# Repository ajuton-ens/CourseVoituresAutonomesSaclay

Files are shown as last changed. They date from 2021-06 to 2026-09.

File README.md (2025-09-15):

# Course de Voitures Autonomes Paris-Saclay CoVAPSy
Ce dépôt regroupe les documents et ressources liées à la course de voitures autonomes 1/10ème de Paris Saclay : https://ajuton-ens.github.io/CourseVoituresAutonomesSaclay/

Il est possible de s'inscrire ou d'obtenir plus d'informations en envoyant un mail à : anthony.juton@ens-paris-saclay.fr 

Le dossier _Simulator_ propose un simulateur Webots R2023b avec une voiture TT-02 équipée d'un lidar.
L'Efrei a aussi déposé un simulateur Webots.

Les cartes électroniques (pdf et fichiers Eagle) et les pièces mécaniques (fichiers step) de la voiture type sont dans le dossier _Hardware_.

---------------------------------------------
# Autonomous Car Race Paris-Saclay CoVAPSy

This repository contains documents and resources related to the 1/10th self-driving car race in Paris-Saclay: https://ajuton-ens.github.io/CourseVoituresAutonomesSaclay/

You can register or obtain more information by sending an email to: anthony.juton@ens-paris-saclay.fr

The folder _Simulator_ includes a Webots R2023b simulator with a TT-02 car equipped with a lidar.
Efrei has also submitted a Webots simulator.

The electronic boards (PDF and Eagle files) and mechanical parts (Step files) for the typical car are in the folder _Hardware_.

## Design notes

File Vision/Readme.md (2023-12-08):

# Dossier regroupant les expériences sur la vision : algorithmes et caméras

# Caméra RPI2
Fonctionne bien avec RPI4 et Jetson nano (connecteur pour caméra RPI sur la JN30D).

# Realsense 435i
Caméra RGBD

# Huskylens
Caméra avec l'IA intégré. C'est très fermé et il est difficile de faire autre chose que les exemples fournis. Résultats décevant sur son exploitation pour les voitures en 2023

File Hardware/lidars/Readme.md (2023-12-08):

# Document recensant les expériences Lidar

## Slamtec RpLidar A2M8
115200 bauds, 10 tours/seconde, 200 points par tour en mode express scan avec le module python rplidar-roboticia
Juste 80 points par tour en mode scan normal.
Attention, le lidar envoyant en continu, il faut recevoir en continu, sous peine de laisser le buffer de réception déborder.

## Slamtec RpLidar A2M12
256000 bauds, 10 tours/seconde, 300 points par tour en mode express scan avec le module python rplidar-roboticia

## Slamtec RpLidar A3M12
tourne plus vite, pas testé

## Slamtec RpLidar S2
1 Mbit/s trop de données pour être utilisé en python. Résultats prometteurs avec le noeud ROS2 associé (écrit en C/C++ certainement).

## Slamtec RpLidar S3
tourne plus vite, pas testé

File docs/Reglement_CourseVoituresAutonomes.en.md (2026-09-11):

# Paris-Saclay Autonomous Car Race Rules (CoVAPSy)

These rules evolve from year to year; feel free to send your comments and suggestions.

## The Vehicle

The vehicle must use a Tamiya TT02 chassis/motor kit and, for propulsion, a NiMH 7.2V battery with a maximum capacity of 5000 mAh. A secondary battery, of any type, is allowed to power the electronics. Powering the motor with a voltage higher than the battery voltage is not allowed. The car must have a body covering more than 80% of it (estimated by the jury in a non-scientific way...).
The vehicle, with all its sensors and actuators, must fit within the dimensions below:

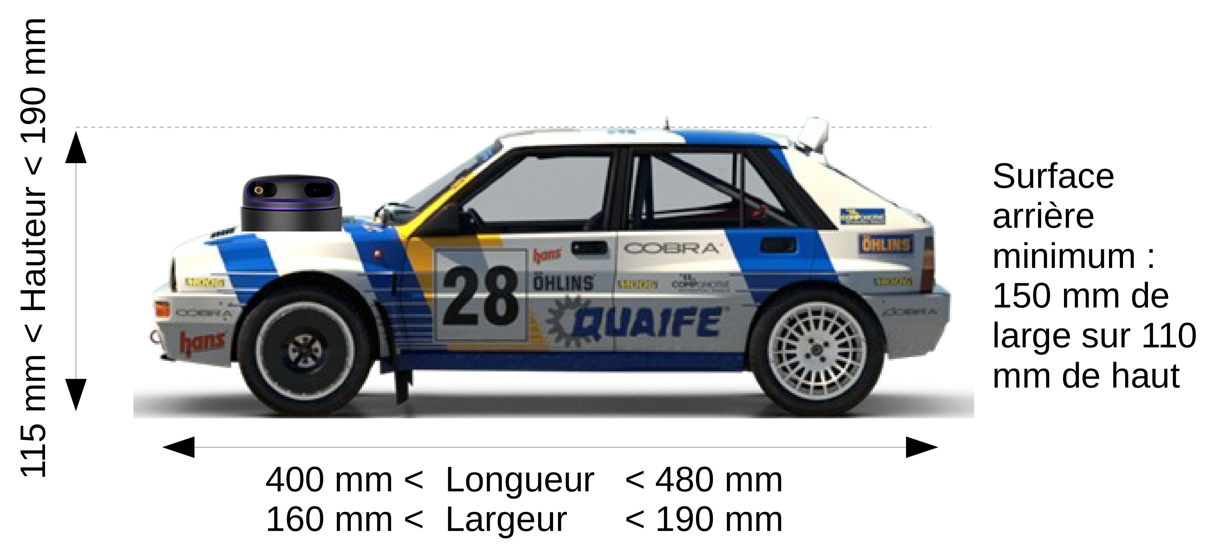
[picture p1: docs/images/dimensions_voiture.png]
car dimensions diagram


The car must be visible to vehicles following it: the car must have at least one opaque rectangle at the rear, 150 mm wide and 110 mm high. Only a small gap (< 10 mm high) for ground clearance is allowed.
Transparent bodies or those with green, red, or gray as the main color are not allowed. Guides for painting the car are available on YouTube (e.g., https://www.youtube.com/watch?v=MO5J6AqEpbs). A test with an RP-Lidar A2M12 or A2M8 validates the rear visibility of the car. If not detected (some black paints absorb infrared), off-white tape will be added to the rear of the car.

It is possible to remove the front-wheel drive to improve turning radius.

The car must be able to operate in both forward and reverse.

To improve steering mechanics, some plastic parts may be replaced with commercially available aluminum parts (Yeah Racing TATT-S03BU available at Rcmart.com or Tamiya kit 54574 sold at Conrad).
Any major modification to the chassis (beyond a few drillings) must be requested and approved by the other institutions participating in the race. The request must include references or plans of the intended modifications.

Team communication with the vehicle must be limited to sending a start signal and a stop signal. The vehicle may send information to the team (telemetry). Sending commands that modify the vehicle's behavior will result in team disqualification. For the 2026 edition, the use of a trackside computer is permitted at the end of remote calculations. Obviously, teams cannot touch this computer once the start has been announced..

A standard car kit is available (see *Standard Car* menu) from the Ménagerie Technologique.

## The Track

The track layout is not known before the day of the competition. Providing the car with information about the track layout is prohibited. Referees may check this, for example, on an auxiliary track. The car may learn the track by completing up to 3 setup laps.

The track consists of 200 mm high borders, green on the right in the direction of travel and red on the left in one direction, and vice versa in the opposite direction. These borders are made of straight elements and arcs with a curvature radius R = 400 mm or more. The floor is gray linoleum. The track is at all points wider than 700 mm but may contain obstacles inside.

Color references:

* GREEN: RAL 6024
* RED: RAL 3020
* FLOOR: PVC GERFLOR concrete effect leone anthracite l.4 m Ref 83309786 (Leroy Merlin)

Color references are approximate, and the track edges may be marked by impacts.

Here is an example of one of the 2023 tracks:

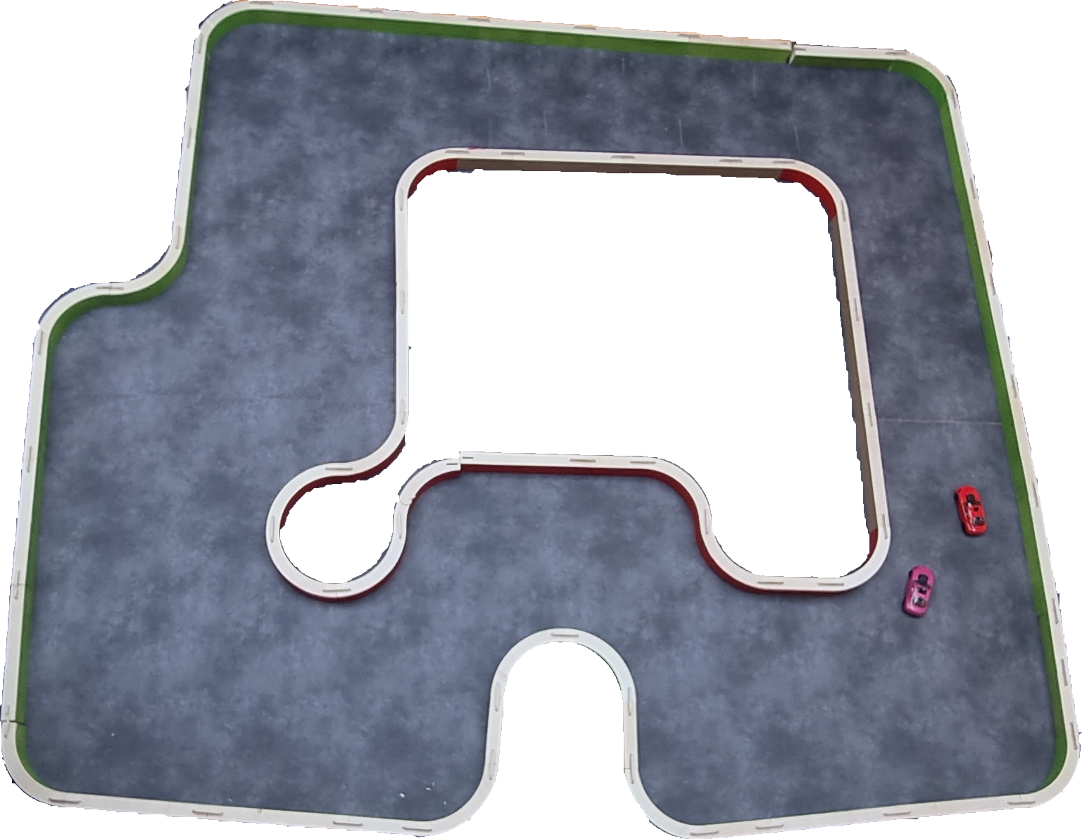
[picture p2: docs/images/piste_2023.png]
example track layout


A track kit is available from the Ménagerie Technologique.

## Homologation

Homologation is done in 4 steps:

* validation of vehicle elements (dimensions, battery, chassis, lidar-detectable color, etc.),
* validation of remote start and stop,
* verification of the vehicle's ability to move along a straight track section plus a curve without touching the borders,
* verification of the vehicle's ability to reverse in case of blockage against an obstacle and in the absence of a vehicle behind.
* verification of the vehicle's ability to avoid an obstacle (with the size of a car) on a section of track.

The referees may consider homologation with a penalty for minor rule violations: for example, a vehicle that does not stop or reverse properly.

For both races and qualifications, a car using SLAM may complete up to 3 setup laps, without obstacles. Obstacles or opponent cars are added afterward, once the car is on the starting grid.

## Qualifications 1 – Time Trial

The first qualification phase consists of 2 runs with a single car on track A, which includes fixed obstacles similar in size to a car.
For each run, the car completes 2 laps. The best of the 2 times is kept, to compensate for any technical issue during the first run. One of the passages is clockwise and the second is counterclockwise.

If the car fails to complete both laps on both attempts, a time of 120 seconds is recorded if the car completed one lap, and 180 seconds if it did not complete even one lap.

At the end of the first qualification phase, the first car gets 25 points, the second 24 points, and so on down to a minimum of 5 points for any car with less than 120 s. A car that has completed just one lap (time of 120s) gets one point.

## Qualifications 2 – Races

The second qualification phase consists of 2 group races with 4 to 8 cars over 3 laps on track B and 3 laps on track C (one clockwise and the other counterclockwise). The method for forming the N groups is based on the qualification ranking (group n is composed of cars ranked n%N, where n is the group number and N is the number of groups). In each race, the car accumulates points for the overall qualification ranking: 10 points for the first, 8 points for the 2nd, 6 for the 3rd, 4 for cars that completed all 3 laps and 1 point for cars that did not finish the race.

For each race (including the final):

* Teams have 3 minutes to set up their vehicle on the track.
* All vehicles in the group are positioned on the starting grid according to qualification results.
* Once all teams have declared they are ready, it is forbidden to touch the vehicles. The referee gives the start signal orally.
* The finishing order is recorded after a predefined number of laps (3 by default for qualification, 5 for finals).
* A car that does not complete the required number of laps is not ranked.

The referee and race marshals ensure the proper conduct of the races:

* A vehicle displaying clearly aggressive behavior towards opponents is disqualified and removed from the track, as is a car deliberately preventing another from overtaking.
* A vehicle immobilized on the track for more than 10 seconds, without being blocked by another car, is removed from the track.
* A vehicle that travels more than 2 m in the wrong direction is removed from the track.

## Final Phases – Races, in 2 Rounds

After the qualifications, each car receives 2 scores:

* the total coursesQualif (sum of points earned in the 2 qualification races)
* the total CLM+courseQualif (the previous score plus the points earned in the time trial qualification).

2 rounds are each composed of 3 races.

The top 2 of each group (by coursesQualif score, with CLM+courseQualif used to break ties) compete in race 1 of each round, the 3rd and 4th in race 2, and the others in race 3. The qualification ranking (by coursesQualif, with CLM+courseQualif as a tiebreaker) determines the starting grid, with the car with the most points starting at the front.

Referees record the finishing order after a predefined number of laps (5 by default) and award points as follows: 25 pts for 1st, 18 pts for 2nd, 15 pts for 3rd, 12 pts for 4th; 10 pts for 5th, 8 pts for 6th; 6 pts for 7th, 4 pts for 8th; 2 pts for 9th and 1 pt for 10th. A car that does not complete the required number of laps gets 0 points. Once the cars in the first race are ranked, points are then awarded to the cars in the second race, and so on.

The final ranking is based only on the points from the 2 final races. In case of a tie, the CLM+courseQualif score is used for the final ranking. If there is still a tie, the coursesQualif score is used.

Prizes are awarded to the 1st, 2nd, and 3rd in the overall ranking. There is also an innovation prize and a prize for the top license teams.

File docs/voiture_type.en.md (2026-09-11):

# Standard Car for the Paris-Saclay Autonomous Car Race

A standard car is offered for the autonomous car race. The complete kit and the kit containing {electronic boards, specific mechanical parts} have been available for purchase since January 2023, especially for teams without mechanical and/or electronic manufacturing capabilities.

This standard car is just an example to help teams get started. It is meant to be improved and expanded.

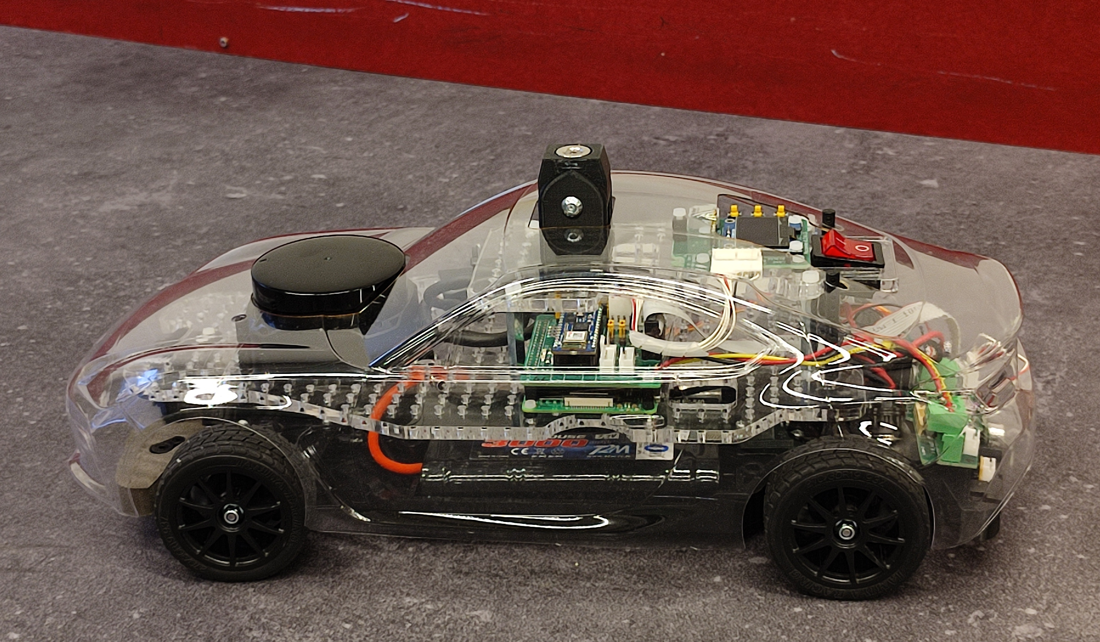
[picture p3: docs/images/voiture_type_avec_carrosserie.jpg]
standard car with body


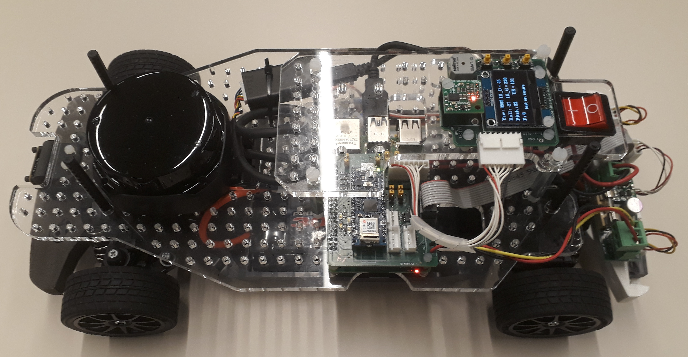
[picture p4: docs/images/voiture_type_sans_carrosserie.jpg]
standard car without body


## Control System

The block diagram of the control system is as follows, with several options for lidars, cameras, single-board computers, or microcontrollers:

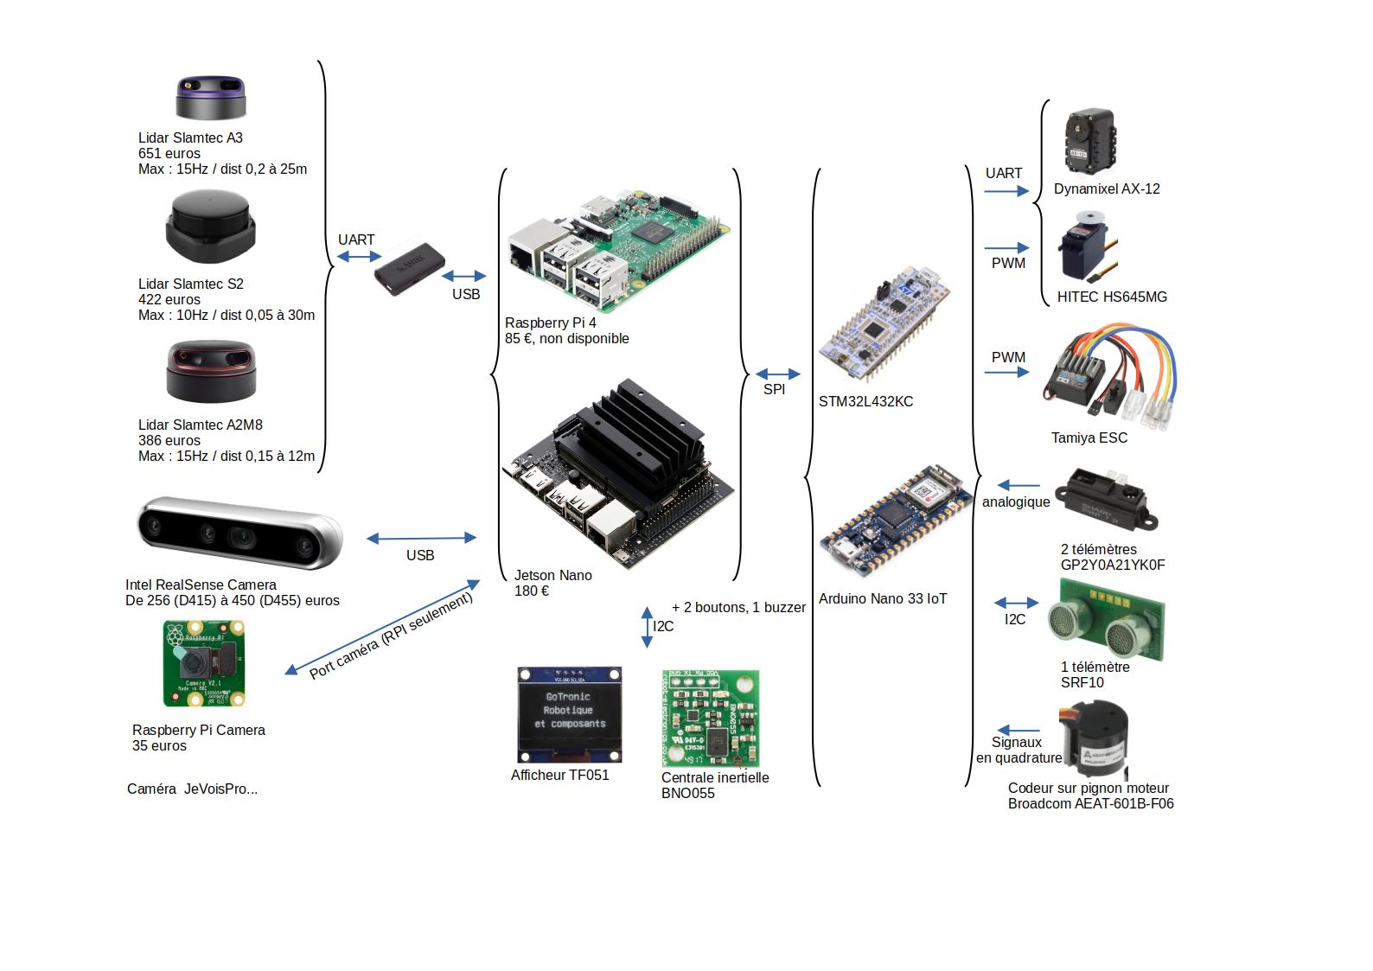
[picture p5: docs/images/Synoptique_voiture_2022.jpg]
block diagram of a standard car


The electronic schematics in Eagle and PDF format are provided in the _Hardware_ folder of the [Git repository](https://github.com/ajuton-ens/CourseVoituresAutonomesSaclay)

## Mechanics

Mechanical parts allow the TT-02 chassis to be adapted to these control system components. STL files are provided in the _Hardware_ folder of the [Git repository](https://github.com/ajuton-ens/CourseVoituresAutonomesSaclay)

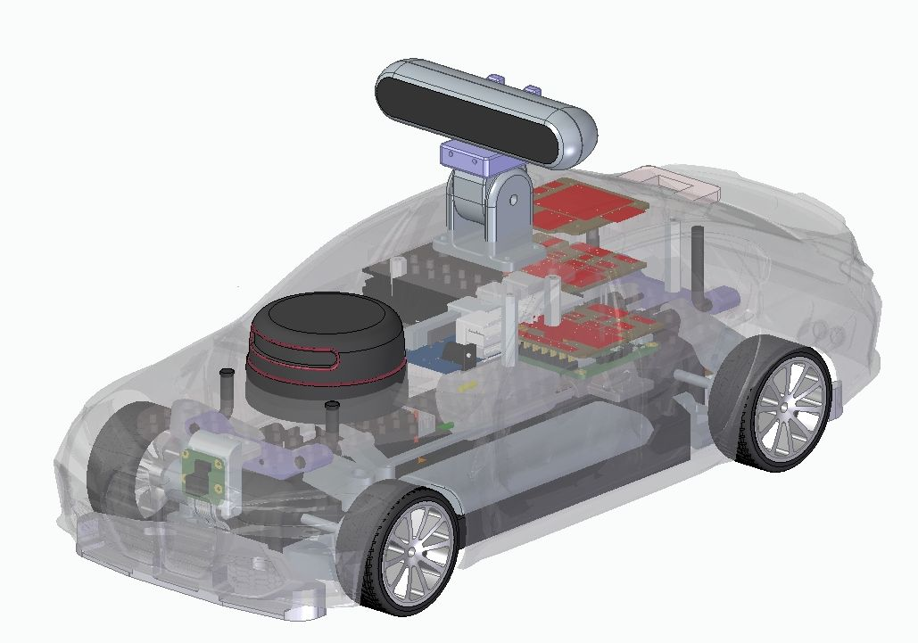
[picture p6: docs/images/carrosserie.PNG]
view with body of the standard car with Realsense camera


In addition to custom bodywork, the main feature of this kit is the modification of the drive shaft gear, the addition of an optical fork, and a new housing to allow measurement of the motor speed.

The kit notably offers the possibility to use a digital AX-12 servo motor instead of the standard analog servo.

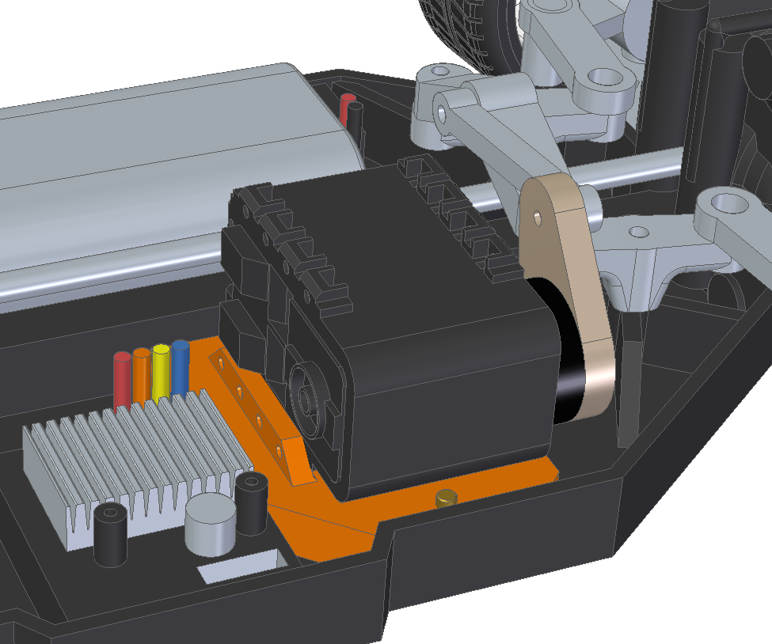
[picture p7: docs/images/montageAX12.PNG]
close-up of the AX-12 servo motor adaptation


Finally, the 3D parts allow for proper mounting of sensors at the front (Raspberry camera) and at the rear (IR and/or ultrasonic rangefinders).

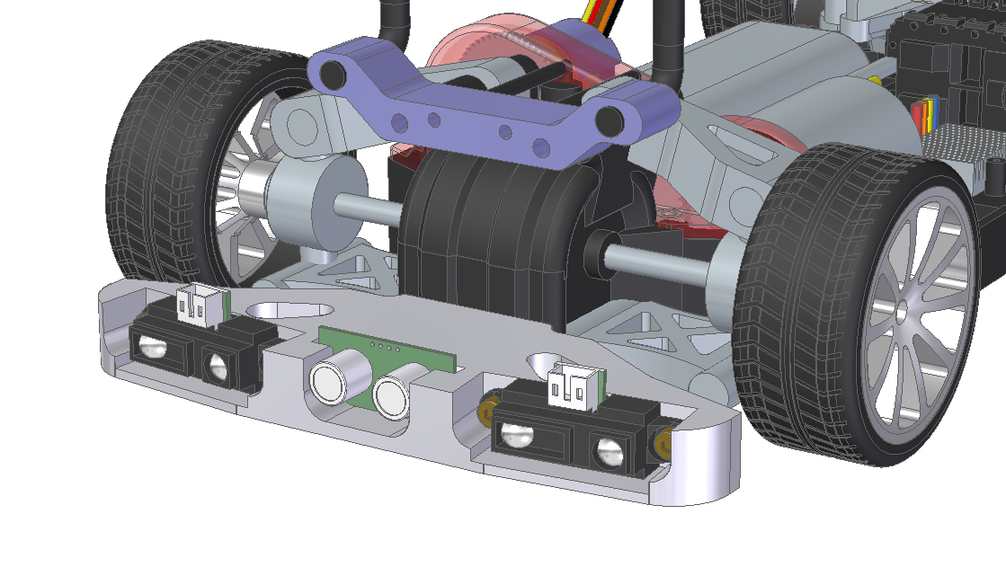
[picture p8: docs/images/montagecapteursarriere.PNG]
close-up of rear sensor mounting


## Parts List 2021

Here is a list of equipment, suppliers, and indicative prices (including VAT).

* Tamiya TT-02 Toyota GR 86 KIT	ref 58694 - RCTeam 58694 - €134.90
* Konect Servo 9kg 0.13s Digital KN-0913LVMG - RCTeam KN-0913LVMG - €19.90
* ORION Charger IQ801 1A - RCTeam ORI30197 - €15.90
* T2M Battery 7.2v Nimh 3000mah - RCTeam T1006300 - €27.30
                                
* Raspberry Pi 4 Model B - Kubii PI48GB - €94.50
* Official Black Micro-HDMI to HDMI Cable 1M - Kubii SC0270 - €4.80
* Micro-SD Card Class 10 32 GB - Kubii KG32_DEL - €8.94
* Official Power Supply for Raspberry Pi 4 15.3W USB-C - Kubii ALIMPI4 - €9.60
* Camera Module v2 8MP - Kubii 2510728 - €25.80
* Ribbon Cable for Raspberry Pi Camera 30 cm - Kubii kub1645-PRD - €0.96

* RPLIDAR A2M12 360 Laser Scanner Slamtec A2-M12 - Roboshop RB-Rpk-22 - €269.03
* USBA – microUSB Cable 20 cm - RS 182-8869 - €3.14

* Sonar Module SRF10 Devantech - Roboshop RB-Dev-10 - €36.86
* Absolute Orientation Module 9 DOF BNO055 Devantech - Roboshop RB-Dev-91 - €31.73
* Nucleo-G431KB Microcontroller Board - Farnell 3132398 - €10.89
* RS PRO USB Cable, Micro-USB B to USB A, 0.5m - RS 236-9078 - €2.89	
* Optical Fork with cables OPTEK TECHNOLOGY OPB815WZ - Farnell 1497919 - €5.39

* **Total for off-the-shelf modules**								~€725

## Parts List 2026

* Tamiya TT-02 Ford Mustang GT4 KIT ref 58664 - RCTEAM 58664 - 129,90 €
* Tamiya Pièce de Direction alu TT-02 54752 - RCTEAM 54752 - 67,20 €
* SkyRC Chargeur Nimh eN18 1.2A - RCTeam SK100184-01 - 19,90 €
* Robitronic Chargeur Peak Charger NiMh 1A - RCTEAM R01018 - 15,90 €
* Absima Batterie NIMH 7.2V 4200mAh - RCTeam 4100012 - 2 x 23,90 €

* Raspberry Pi 5 8 Go - Kubii - 204 €
* Ventilateur dissipateur officiel pour Raspberry Pi 5 - Kubii - 6 €
* Câble Micro-HDMI vers HDMI (type A) 1M pour PI4 - Kubii - 4,50 €
* Carte Micro-SD SanDisk Classe 10 - Kubii - 16,20 €
* Module caméra v3 Raspberry Pi grand angle - Kubii - 39 €
* Nappe Cable pour Raspberry Pi Camera 30 cm - Kubii - 2,40 €

* servomoteur HerkuleX DRS-0101 - Roboshop RB-Das-05 - 76,4 €
* SLAMTEC RPLIDAR C1 Scanner Laser DTOF 360°  - Roboshop RB-Rpk-35 - 75,3 €

* Module Sonar SRF10 Devantech - Gotronic 24506 - 19,90 €
* Carte microcontrôleur Nucleo-G431KB - Farnell 3132398 - 17,76 €
* Câble USB RS PRO, Micro-USB B vers USB A, 0.5m - RS 236-9078 - 2,86 €	
* Fourche optique, avec câbles	OPTEK TECHNOLOGY OPB815WZ - Farnell 1497919 - 4,54 €

* **Total for off-the-shelf modules**								~745 €

**Options:**

It is possible to replace the Raspberry Pi single-board computer with a Jetson Orin GPU board. Qualcomm/Thundercomm also offers a similar board, the Rubik Pi 3.

Camera RGBD to be placed on the roof:

* Realsense D435i Camera - Digikey 2311-82635D435IDKMP-ND - €445.54

The Ménagerie Technologique offers all the electronic boards for the standard car for €350 and all the mechanical parts for 250 €.

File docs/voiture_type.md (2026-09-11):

# Voiture type pour la course de voitures autonomes de Paris Saclay

Une voiture type est proposée pour la course de voitures autonomes. Le kit complet et le kit {cartes électroniques, pièces mécaniques spécifiques} sont disponibles à la vente depuis janvier 2023, notamment pour des équipes sans moyens de fabrication mécanique et/ou électronique.

Cette voiture type n'est qu'un exemple pour aider les équipes à démarrer. Il ne demande qu'à être enrichi.

voiture type avec sa carrosserie

voiture type sans sa carrosserie

## Contrôle-commande

Le schéma synoptique de la partie contrôle-commande est le suivant, avec plusieurs possibilités de lidars, caméras, nano-ordinateurs ou micro-contrôleurs : 

synoptique d'une voiture type

Les schémas électroniques au format Eagle et en pdf sont fournis dans le dossier _Hardware_ du [dépôt Git](https://github.com/ajuton-ens/CourseVoituresAutonomesSaclay)

## La mécanique

Des pièces mécaniques permettent d'adapter le châssis TT-02 à ces équipements de contrôle-commande. Les fichiers stl sont fournis dans le dossier _Hardware_ du [dépôt Git](https://github.com/ajuton-ens/CourseVoituresAutonomesSaclay)

vue avec carrosserie de la voiture type avec caméra Realsense

Outre les découpes propres de carrosserie, l'élément majeur de ce kit est la modification de la roue dentée de l'axe de transmission, l'ajout d'une fourche optique et d'un nouveau carter pour permettre la mesure de la vitesse du moteur.

Le kit propose notamment la possibilité d'utiliser un servo-moteur numérique AX-12 à la place du servo-moteur analogique standard.

zoom sur l'adaptation pour servo-moteur AX-12

Enfin, les pièces 3D permettent une fixation propre des capteurs à l'avant (caméra Raspberry) comme à l'arrière (télémètres IR et/ou ultrason).

zoom sur la fixation des capteurs à l'arrière

## Liste du matériel version 2021

Voici une liste de matériel, de fournisseurs et de prix TTC indicatifs.

* Tamiya TT-02 Toyota GR 86 KIT	ref 58694 - RCTeam 58694 - 134,90 €
* Konect Servo 9kg 0.13s Digital KN-0913LVMG - RCTeam KN-0913LVMG - 19,90 €
* ORION Chargeur IQ801 1A - RCTeam ORI30197 - 15,90 €
* T2M Accu 7.2v Nimh 3000mah - RCTeam T1006300 - 27,30 €

* Raspberry Pi 4 modèle B - Kubii PI48GB - 94,50 €
* Câble officiel noir Micro-HDMI vers HDMI 1M - Kubii SC0270 - 4,80 €
* Carte Micro-SD Classe 10 32 GB - Kubii KG32_DEL - 8,94 €
* Alimentation Officielle pour Raspberry Pi 4 15.3W USB-C - Kubii ALIMPI4 - 9,60 €
* Module Caméra v2 8MP - Kubii 2510728 - 25,80 €
* Nappe Cable pour Raspberry Pi Camera 30 cm - Kubii kub1645-PRD - 0,96 €

* Scanner à distance laser RPLIDAR A2M12 360 Slamtec A2-M12 - Roboshop RB-Rpk-22 - 269,03 €
* Câble USBA – microUSB 20 cm - RS 182-8869 - 3,14 €

* Module Sonar SRF10 Devantech - Roboshop RB-Dev-10 - 36,86 €
* Module d'Orientation Absolue 9 DOF BNO055	Devantech - Roboshop RB-Dev-91 - 31,73 €
* Carte microcontrôleur Nucleo-G431KB - Farnell 3132398 - 10,89 €
* Câble USB RS PRO, Micro-USB B vers USB A, 0.5m - RS 236-9078 - 2,89 €	
* Fourche optique, avec câbles	OPTEK TECHNOLOGY OPB815WZ - Farnell 1497919 - 5,39 €

* **Total des modules sur étagère**								~725 €

## Liste du matériel version 2026

* Tamiya TT-02 Ford Mustang GT4 KIT ref 58664 - RCTEAM 58664 - 129,90 €
* Tamiya Pièce de Direction alu TT-02 54752 - RCTEAM 54752 - 67,20 €
* SkyRC Chargeur Nimh eN18 1.2A - RCTeam SK100184-01 - 19,90 €
* Robitronic Chargeur Peak Charger NiMh 1A - RCTEAM R01018 - 15,90 €
* Absima Batterie NIMH 7.2V 4200mAh - RCTeam 4100012 - 2 x 23,90 €

* Raspberry Pi 5 8 Go - Kubii - 204 €
* Ventilateur dissipateur officiel pour Raspberry Pi 5 - Kubii - 6 €
* Câble Micro-HDMI vers HDMI (type A) 1M pour PI4 - Kubii - 4,50 €
* Carte Micro-SD SanDisk Classe 10 - Kubii - 16,20 €
* Module caméra v3 Raspberry Pi grand angle - Kubii - 39 €
* Nappe Cable pour Raspberry Pi Camera 30 cm - Kubii - 2,40 €

* servomoteur HerkuleX DRS-0101 - Roboshop RB-Das-05 - 76,4 €
* SLAMTEC RPLIDAR C1 Scanner Laser DTOF 360°  - Roboshop RB-Rpk-35 - 75,3 €

* Module Sonar SRF10 Devantech - Gotronic 24506 - 19,90 €
* Carte microcontrôleur Nucleo-G431KB - Farnell 3132398 - 17,76 €
* Câble USB RS PRO, Micro-USB B vers USB A, 0.5m - RS 236-9078 - 2,86 €	
* Fourche optique, avec câbles	OPTEK TECHNOLOGY OPB815WZ - Farnell 1497919 - 4,54 €

* **Total des modules sur étagère**								~745 €

**Options :**

Il est possible de remplacer le nano-ordinateur Raspberry Pi par une carte GPU Jetson Orin. 

Qualcomm/Thundercomm propose aussi une carte similaire, la rubik Pi 3

Caméra RGBD à placer sur le toit : 

* Caméra Realsense D435i - Digikey 2311-82635D435IDKMP-ND - 445,54 €

La ménagerie technologique propose l'ensemble des cartes électroniques de la voiture type pour 350 € et l'ensemble des pièces mécaniques pour 250 €

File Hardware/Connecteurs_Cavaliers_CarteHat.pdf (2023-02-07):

Origine de l’alimentation 3V3 :
A gauche, elle est issue de la carte microcontrôleur (à utiliser si il n’y a

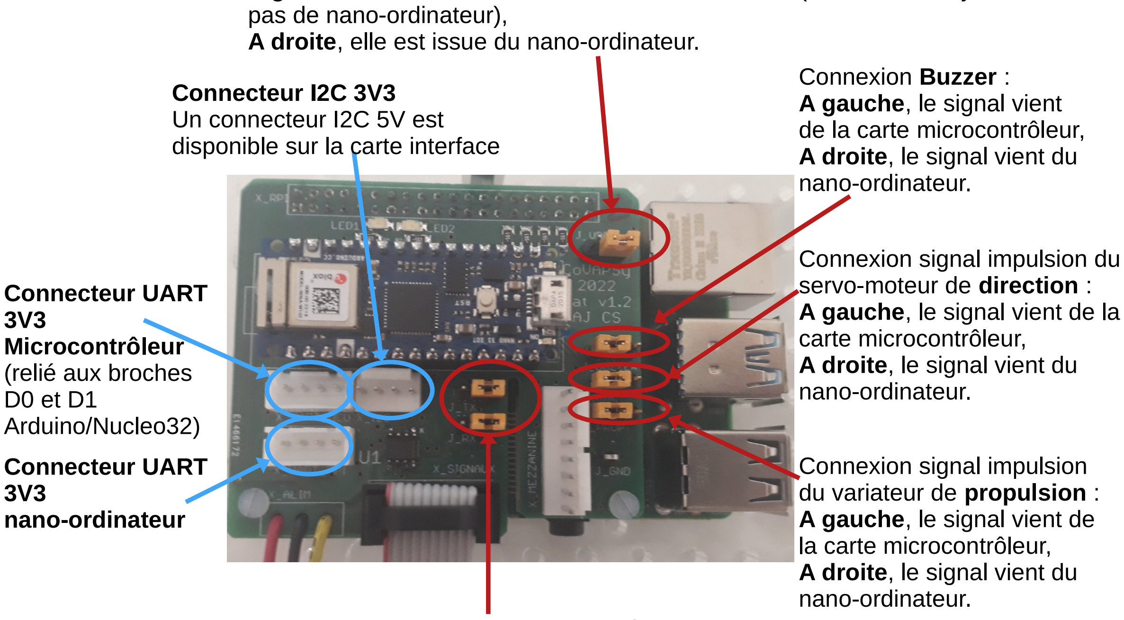
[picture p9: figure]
pas de nano-ordinateur),; Connexion Buzzer :; A gauche, le signal vient; de la carte microcontrôleur,; A droite, le signal vient du; nano-ordinateur.; Connexion signal impulsion du; servo-moteur de direction :; A gauche, le signal vient de la; carte microcontrôleur,; Connexion signal impulsion; du variateur de propulsion :; A gauche, le signal vient de; la carte microcontrôleur,; Connecteur I2C 3V3; Un connecteur I2C 5V est; disponible sur la carte interface; Connecteur UART; Microcontrôleur; (relié aux broches; Arduino/Nucleo32); nano-ordinateur

A droite, elle est issue du nano-ordinateur.

## Connecteurs et cavaliers de la carte Hat

Cette fiche présente le rôle de chacun des connecteurs et cavaliers de la carte Hat.
- On nomme carte microcontrôleur la carte Arduino ou Nucleo32 connectée sur la carte Hat,
- On nomme nano-ordinateur la carte Raspberry Pi ou Jetson nano située sous la carte Hat.

Remarques :

- Pour contrôler le servo-moteur de direction depuis le nano-ordinateur, il faut s’assurer d’utiliser les sorties PWM Hardware. Pour la raspberry Pi, on trouve les infos par exemple sur https://pypi.org/project/rpi-hardware-pwm/ , pour la Jetson nano, c’est plus compliqué… La solution est la bienvenue !
- Si on souhaite réaliser un asservissement de vitesse, pour rendre la vitesse indépendante de la tension de la batterie, le microcontrôleur est plus approprié : mode capture du timer pour une lecture précise de la vitesse, sortie PWM hardware, simplicité à appeler une fonction d’interruption périodiquement pour l’asservissement. Il est alors utile de placer le cavalier J_Prop à gauche.
- Le connecteur UART 3V3 du microcontrôleur peut servir pour connecteur le port UART du Lidar directement au microcontrôleur (sans passer par le boîtier de conversion UART ↔ USB). Dans ce cas, il faut alimenter le signal PWM de commande de la vitesse du lidar en 3V3.
- Il est possible qu’il y ait une inversion Tx ↔ Rx au niveau du connecteur HerkuleX de la carte Interface. A vérifier...

Origine des signaux UART Rx et Tx reliés sur la nappe (vers la carte interface et les connecteurs pour servo-moteurs numériques)
A gauche, les signaux sont connectés à la carte microcontrôleur,
A droite, les signaux sont connectés au nano-ordinateur.

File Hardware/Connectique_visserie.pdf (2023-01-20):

## Connecteur JST

## PH 2.54 mm vers

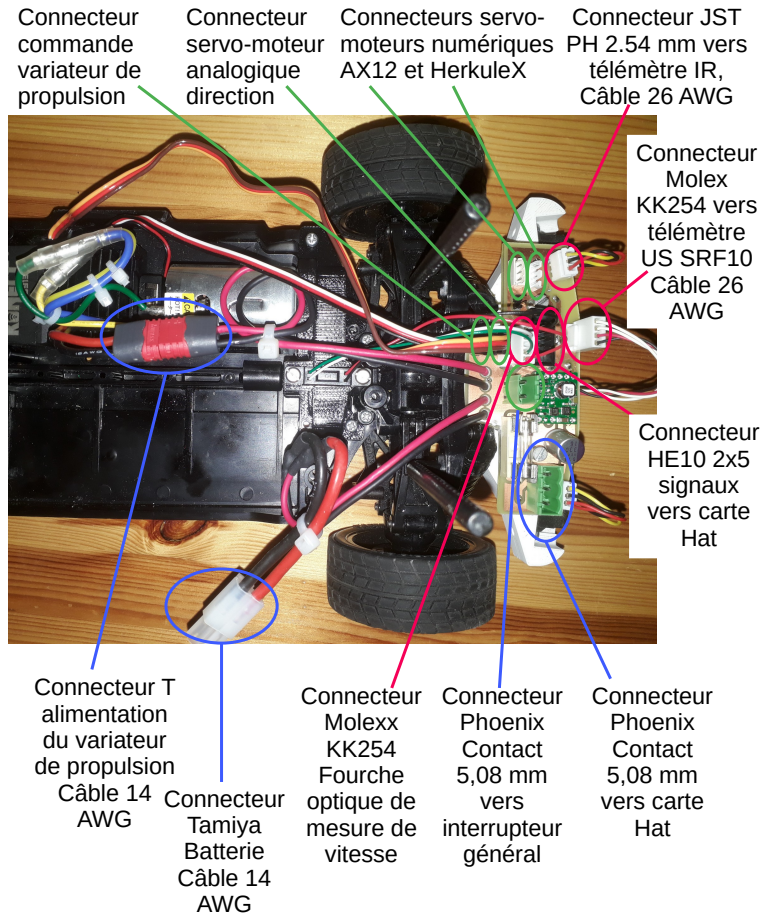
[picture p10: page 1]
Connecteur; Tamiya; Batterie; Câble 14; AWG; Phoenix; Contact; vers carte; Hat; télémètre IR,; Câble 26 AWG; Connecteurs servo-; moteurs numériques; AX12 et HerkuleX; Molex; KK254 vers; télémètre; US SRF10; Câble 26; signaux; vers; interrupteur; général; servo-moteur; analogique; direction; commande; variateur de; propulsion; Molexx; Fourche; optique de; mesure de; vitesse; Connecteur T; alimentation; du variateur; de propulsion

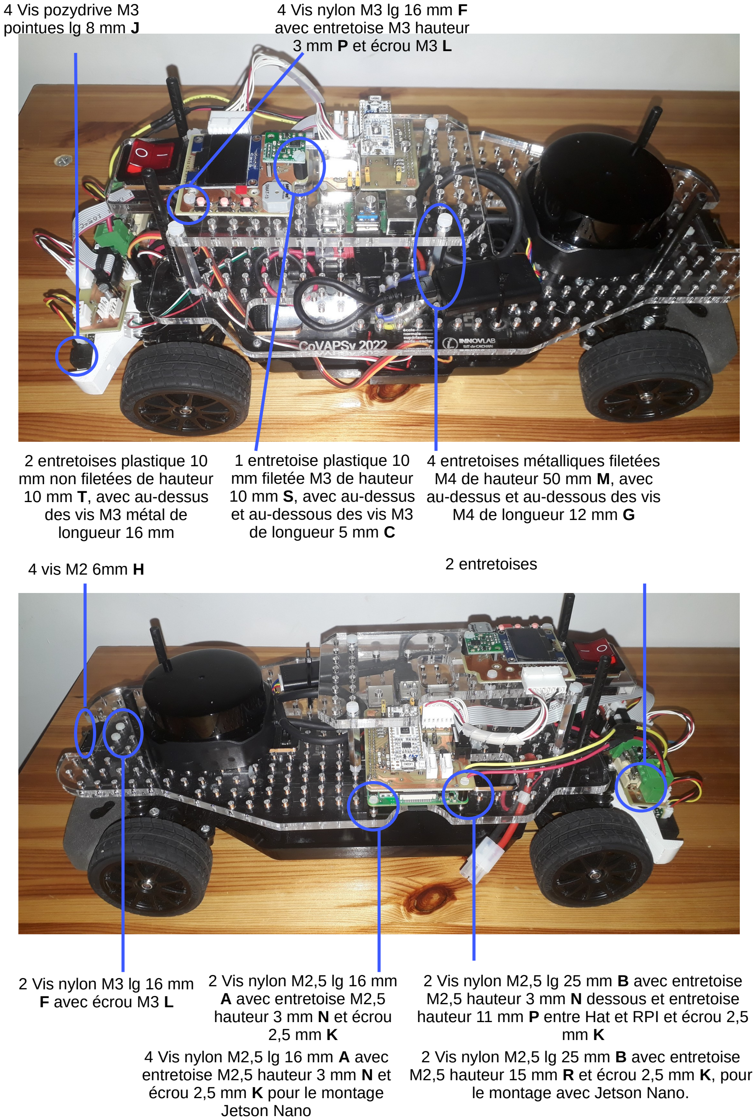
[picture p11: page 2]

2 Vis nylon M2,5 lg 16 mm
A avec entretoise M2,5
hauteur 3 mm N et écrou
2,5 mm K

2 Vis nylon M2,5 lg 25 mm B avec entretoise M2,5 hauteur 3 mm N dessous et entretoise hauteur 11 mm P entre Hat et RPI et écrou 2,5 mm K

4 entretoises métalliques filetées M4 de hauteur 50 mm M, avec au-dessus et au-dessous des vis M4 de longueur 12 mm G

1 entretoise plastique 10
mm filetée M3 de hauteur
10 mm S, avec au-dessus
et au-dessous des vis M3
de longueur 5 mm C

2 Vis nylon M3 lg 16 mm
F avec écrou M3 L

4 vis M2 6mm H

4 Vis nylon M3 lg 16 mm F
avec entretoise M3 hauteur 3 mm P et écrou M3 L

4 Vis pozydrive M3
pointues lg 8 mm J

2 entretoises

2 entretoises plastique 10 mm non filetées de hauteur 10 mm T, avec au-dessus
des vis M3 métal de
longueur 16 mm

2 Vis nylon M2,5 lg 25 mm B avec entretoise M2,5 hauteur 15 mm R et écrou 2,5 mm K, pour le montage avec Jetson Nano.

4 Vis nylon M2,5 lg 16 mm A avec entretoise M2,5 hauteur 3 mm N et écrou 2,5 mm K pour le montage Jetson Nano

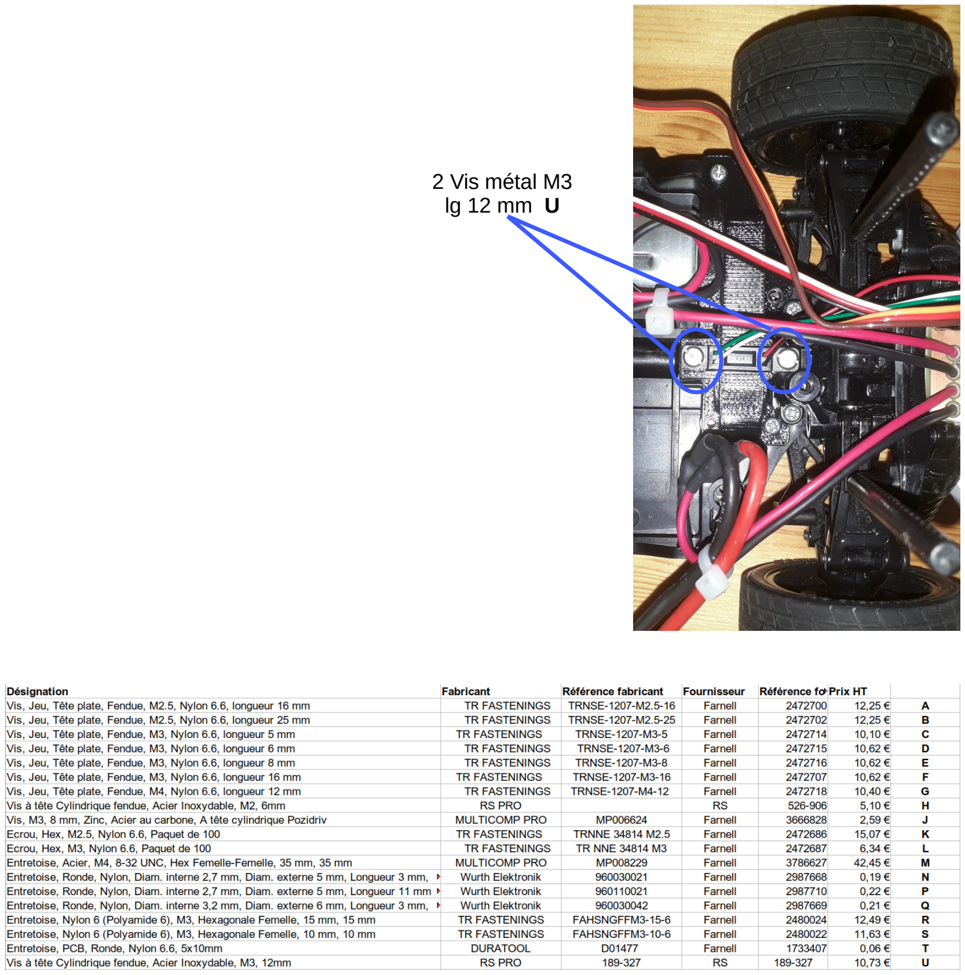
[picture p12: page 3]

2 Vis métal M3
lg 12 mm U

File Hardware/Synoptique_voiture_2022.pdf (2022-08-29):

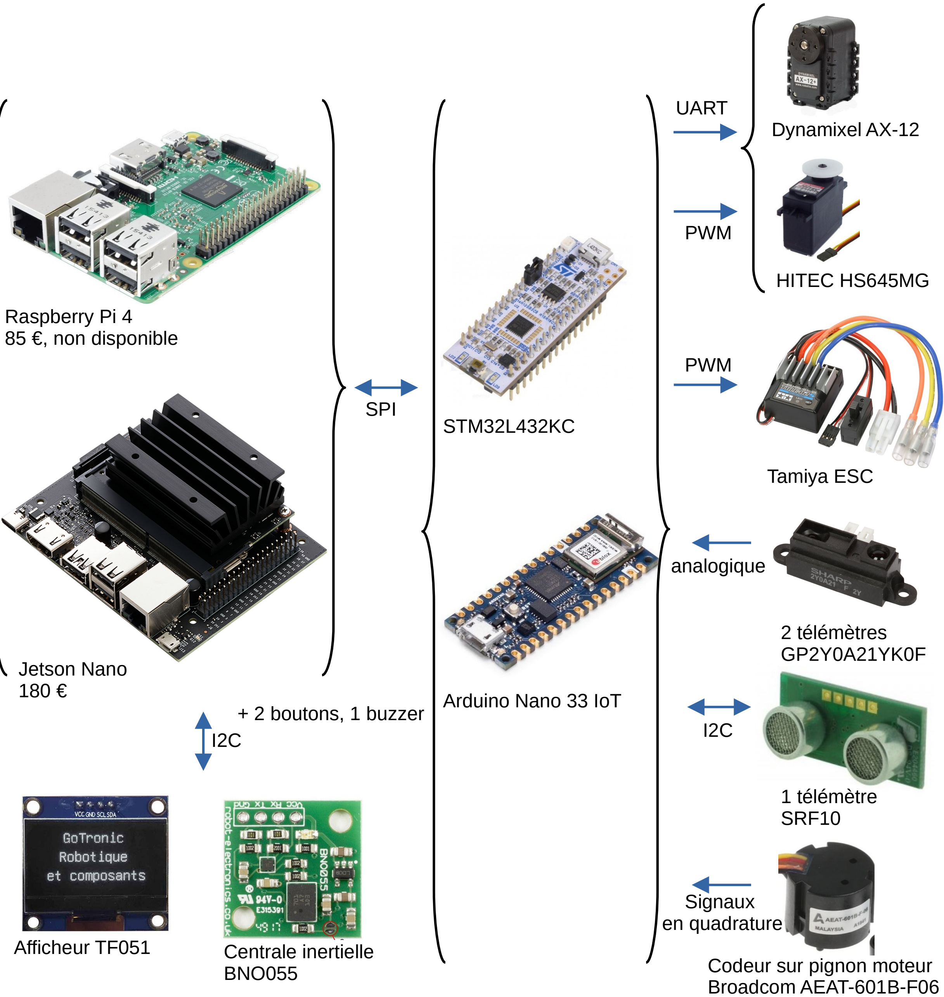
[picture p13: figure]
Raspberry Pi 4 85 €, non disponible; Jetson Nano; SPI; STM32L432KC; Arduino Nano 33 IoT; PWM; analogique; HITEC HS645MG; Tamiya ESC; UART; 2 télémètres; Dynamixel AX-12; 1 télémètre; SRF10; Afficheur TF051; Centrale inertielle; BNO055; + 2 boutons, 1 buzzer; Codeur sur pignon moteur; Broadcom AEAT-601B-F06; Signaux; en quadrature
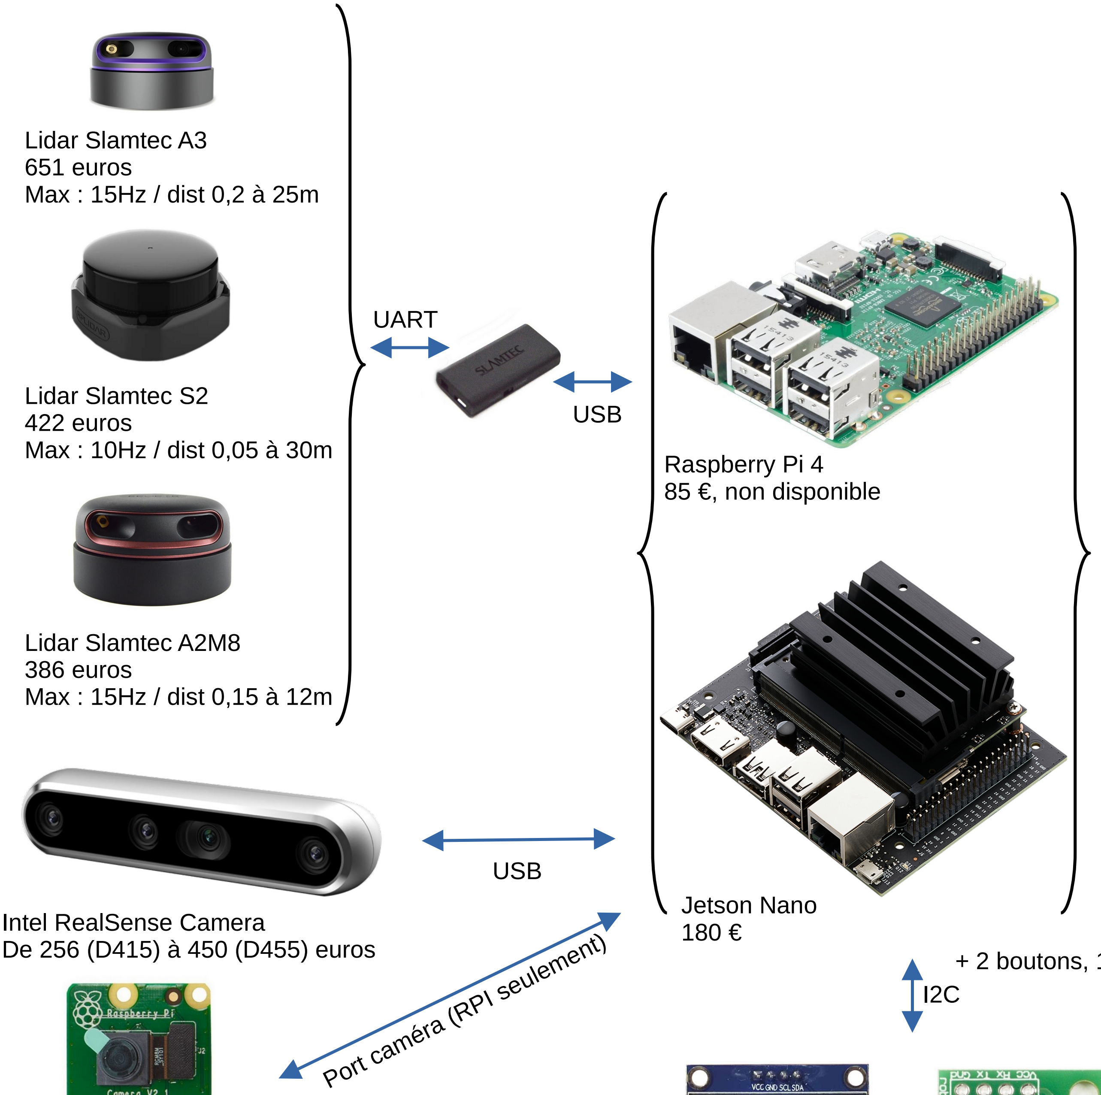
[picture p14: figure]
Lidar Slamtec A2M8 386 euros; Max : 15Hz / dist 0,15 à 12m; Lidar Slamtec S2; 422 euros Max : 10Hz / dist 0,05 à 30m; Lidar Slamtec A3 651 euros; Max : 15Hz / dist 0,2 à 25m; USB; UART; Intel RealSense Camera De 256 (D415) à 450 (D455) euros; Port caméra (RPI seulement)

Raspberry Pi Camera
35 euros

Caméra JeVoisPro...

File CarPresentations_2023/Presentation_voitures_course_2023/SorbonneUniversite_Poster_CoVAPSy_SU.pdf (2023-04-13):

E0

E1 | E2

## Etat 0 - Navigation LiDAR

## Etat 1 - Navigation ToF

## Etat 2 - Demi-Tour

### Utilisation du LiDAR pour la navigation par défaut Algorithme de recherche de meilleure direction par rapport à l’environnement devant soi Commande de braquage avec contrôleur en Avance de Phase

### Utilisation des 4 ToF et de la caméra pour déterminer la manœuvre à exécuter :

### évitement d'obstacle

### manoeuvre de désencombrement

### navigation de secours (panne LiDAR)

### Si la voiture est dirigée dans le mauvais sens la navigation ToF et LiDAR laisse place à une manœuvre de demi-tour

Véhicule autonome basé sur le kit Tamyia TT-02, équipé d'un LiDAR, de 4 ToFS, deux à l'avant et deux à l'arrière et d'une caméra frontale.
Le châssis est entièrement démontable et conçu pour garantir un espace intérieur plus important tout en maintenant une solidité convenable.
Les moteurs, le Raspberry Pi 3, l'Arduino et les capteurs sont alimentés par une batterie de puissance et une batterie portable.
Pour des raisons pratiques, le bouton pressoir sur le toit du véhicule fait office de On/Off sur le moteur de puissance.

# Description générale

# Navigation avec ROS et Machine à État

La navigation du véhicule est basée sur une machine à état (MAE) qui garantit une meilleure autonomie et robustesse du système aux différents contextes rencontrés. Les transitions d’états sont actionnées par des flags récupérés sur les topics spécifiques à chaque nœud d’état. Ce système de MAE permet une meilleure gestion des ressources. En effet, un nœud consomme des ressources computationnelles UNIQUEMENT si il est actif ce qui permet d’implémenter des algorithmes plus complexes sans sacrifier en performance.

### Commandes de vitesse et braquage avec contrôleur proportionnel

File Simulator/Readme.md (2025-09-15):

# Démarrer avec Webots
Plusieurs équipes utilisent le logiciel de simulation Webots version R2025a pour la saison 2025-2026.

Pour commencer avec Webots, il est bon de lire au minimum le guide de démarrage rapide :
https://www.cyberbotics.com/doc/guide/getting-started-with-webots

Et de faire au minimum les tutoriaux 1, 2, 3, 4, 5 et 8 :
https://www.cyberbotics.com/doc/guide/tutorials

Le dossier compressé _Simulateur_CoVAPSy_Webots2025a_Base.zip_ contient une piste simple avec 3 voitures TT-02 (un sparring partner, une voiture programmée en C et une en python) ainsi que des éléments pour faire des pistes différentes.

Sur Culture Science de l'ingénieur se trouve un article pédagogique pour démarrer : [CoVAPSy, mise en oeuvre du simulateur webots](https://sti.eduscol.education.fr/si-ens-paris-saclay/ressources_pedagogiques/covapsy-mise-en-oeuvre-du-simulateur-webots)

Pour modifier la piste. Le premier groupe contient les 6 éléments _solid_ de base (droit_1m, droit_50_cm et virage, en vert et en rouge) :

* Copier/Coller du premier groupe au second permet d'ajouter un élément
* Une fois le _solid_ sélectionné dans la vue 3D, les flèches verte et rouge permettent de le déplacer. La flèche "rotation" bleue permet de le faire tourner.
* Après avoir positionné l'élément grossièrement sur la piste, le champ _translation_ permet de le positionner finement. Un multiple de 0,25 m dans les champs x et y permet un bon alignement des éléments.

Pour partager une nouvelle piste, envoyer le fichier wbt à anthony.juton@ens-paris-saclay.fr

--------------------------------------------
# Getting Started with Webots

Several teams use the Webots simulation software, version R2025a, for the 2025-2026 season.

To get started with Webots, it is recommended to read at least the quick start guide:
https://www.cyberbotics.com/doc/guide/getting-started-with-webots

And to complete at least tutorials 1, 2, 3, 4, 5, and 8:
https://www.cyberbotics.com/doc/guide/tutorials

The compressed folder _Simulateur_CoVAPSy_Webots2025a_Base.zip_ contains a simple track with 3 TT-02 cars (a sparring partner, one car programmed in C, and one in Python) as well as elements to create different tracks.

A pedagogical article to get started is available on Culture Sciences de l'Ingénieur: [CoVAPSy, implementation of the Webots simulator](https://sti.eduscol.education.fr/si-ens-paris-saclay/ressources_pedagogiques/covapsy-mise-en-oeuvre-du-simulateur-webots)

To modify the track: the first group contains the 6 basic _solid_ elements (droit_1m, droit_50_cm, and virage, in green and red):

* Copy/Paste from the first group to the second to add an element
* Once the _solid_ is selected in the 3D view, the green and red arrows allow you to move it. The blue "rotation" arrow allows you to rotate it.
* After roughly positioning the element on the track, the _translation_ field allows you to fine-tune its position. Using multiples of 0.25 m in the x and y fields ensures good alignment of the elements.

To share a new track, send the wbt file to anthony.juton@ens-paris-saclay.fr

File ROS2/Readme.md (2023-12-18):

# Dossier pour le dépôt des noeuds ROS développés spécifiquement

On peut ajouter sur ce document les noeuds ROS2 testés

## ENS Paris Saclay
Travail sur le SLAM avec un noeud ROS pour la vision, un noeud pour le SLAM (MTAB) et un noeud à développer pour l'envoi des consignes de direction et vitesse

## Sorbonne Université 
Le dépôt du projet ROS2 2023 de Sorbonne Université : https://github.com/eliot-christon/course_2023_pkg

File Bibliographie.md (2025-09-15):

# Bibliographie

Chacun peut y ajouter les sources qui lui semblent intéressantes, avec une brève description.

* Pour démarrer avec la voiture CoVAPSy, plusieurs articles sont disponibles sur Culture Sciences de l'ingénieur :

  * Course Voitures Autonomes Paris Saclay (CoVAPSy) : Travaux pratiques autour des voitures autonomes https://sti.eduscol.education.fr/si-ens-paris-saclay/ressources_pedagogiques/covapsy-tp-autour-des-voitures-autonomes

  * CoVAPSy : Mise en œuvre du simulateur Webots https://sti.eduscol.education.fr/si-ens-paris-saclay/ressources_pedagogiques/covapsy-mise-en-oeuvre-du-simulateur-webots

  * CoVAPSy : Premiers programmes python sur la voiture réelle https://sti.eduscol.education.fr/si-ens-paris-saclay/ressources_pedagogiques/covapsy-premiers-programmes-python-sur-voiture-reelle

  * CoVAPSy : Premiers programmes en langage C sur la voiture réelle https://sti.eduscol.education.fr/si-ens-paris-saclay/ressources_pedagogiques/covapsy-premiers-programmes-langage-c-sur-la-voiture-reelle

* Pour une introduction à l'Intelligence Artificielle et notamment à l'apprentissage par renforcement : 
https://eduscol.education.fr/sti/si-ens-paris-saclay/ressources_pedagogiques/dossier-intelligence-artificielle

* Un exemple documenté de mise en oeuvre de l'apprentissage par renforcement sur les voitures CoVAPSy : Apprentissage par renforcement et transfert simulation vers réalité pour la conduite de voitures autonomes https://sti.eduscol.education.fr/si-ens-paris-saclay/ressources_pedagogiques/apprentissage-renforcement-transfert-simulation-vers-realite-pourla-conduite-voitures-au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

* La playlist de F1Teenth avec ROS, SLAM, filtre à particules et FollowTheGap : https://www.youtube.com/playlist?list=PL868twsx7OjdnroeAUFVBGlKGnFGi9txc

-------------------------------------------------
# Bibliography

Anyone can add any sources they find interesting, along with a brief description.

* To get started with the CoVAPSy car, several articles are available (in French) on Culture Sciences de l'ingénieur:

  * Paris-Saclay Autonomous Car Race (CoVAPSy): Practical work on autonomous cars https://sti.eduscol.education.fr/si-ens-paris-saclay/ressources_pedagogiques/covapsy-tp-autour-des-voitures-autonomes

  * CoVAPSy: Implementation of the Webots simulator https://sti.eduscol.education.fr/si-ens-paris-saclay/ressources_pedagogiques/covapsy-mise-en-oeuvre-du-simulateur-webots

  * CoVAPSy: First Python programs on the real car https://sti.eduscol.education.fr/si-ens-paris-saclay/ressources_pedagogiques/covapsy-premiers-programmes-python-sur-voiture-reelle

  * CoVAPSy: First C Programs on Real Cars https://sti.eduscol.education.fr/si-ens-paris-saclay/ressources_pedagogiques/covapsy-premiers-programmes-langage-c-sur-la-voiture-reelle

* For an introduction to Artificial Intelligence, particularly reinforcement learning:
https://eduscol.education.fr/sti/si-ens-paris-saclay/ressources_pedagogiques/dossier-intelligence-artificielle

* A documented example of implementing reinforcement learning on cars: CoVAPSy: Reinforcement Learning and Simulation-to-Reality Transfer for Driving Self-Driving Cars https://sti.eduscol.education.fr/si-ens-paris-saclay/ressources_pedagogiques/apprentissage-renforcement-transfert-simulation-vers-realite-pourla-conduite-voitures-au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

* The F1Teenth playlist with ROS, SLAM, particle filter, and FollowTheGap: https://www.youtube.com/playlist?list=PL868twsx7OjdnroeAUFVBGlKGnFGi9txc

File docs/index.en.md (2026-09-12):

# Paris-Saclay Autonomous Car Race

Since 2020, the event has welcomed teams of students (from IUTs, engineer schools, universities) for a 1/10th scale autonomous car race, in a friendly and collaborative spirit. The prospect of final victory does not prevent teams from helping each other throughout the year with the aim of making collective progress.

The 1/10th scale autonomous cars are a fantastic platform for hands-on experimentation with artificial intelligence. Reinforcement learning, supervised learning, imitation learning, unsupervised learning—AI in all its forms meets in Saclay every April.

Feel free to join the competition!

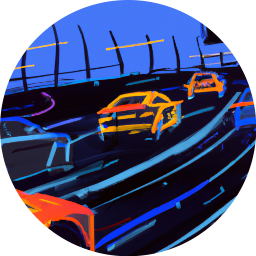
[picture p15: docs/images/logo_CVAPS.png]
autonomous car race logo


## 2027 Edition Date

The 2027 edition will take place on Saturday, April 3rd at ENS Paris-Saclay.

## Previous Editions

Summaries and videos from previous editions, as well as guides to get started (first Python programs, getting started with the simulator, reinforcement learning, ROS2...) are available on the Culture Sciences de l'Ingénieur website: [CoVAPSy Documents](https://sti.eduscol.education.fr/si-ens-paris-saclay/actualites/course-voitures-autonomes-paris-sacaly-2025)

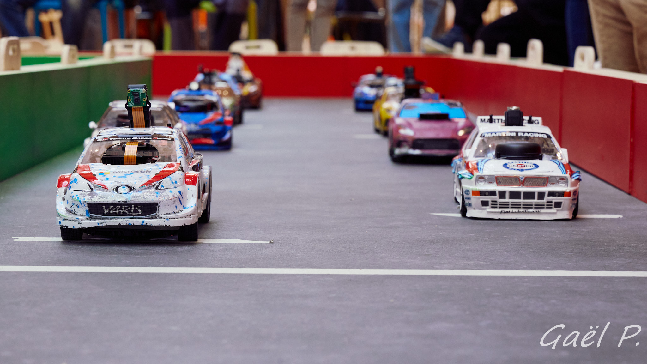
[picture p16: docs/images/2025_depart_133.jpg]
photo of the 2025 race


## Git

The [Git repository](https://github.com/ajuton-ens/CourseVoituresAutonomesSaclay) provides the rules, some photos and videos, a bibliography, and all the resources needed to participate in the Paris-Saclay autonomous car race, as well as a place to share

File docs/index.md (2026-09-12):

# Course de Voitures Autonomes de Paris-Saclay

L'événement accueille depuis 2020 des équipes d'étudiants (IUT, écoles d'ingénieurs, universités) pour une course de voitures 1/10ème autonomes, dans un esprit convivial et de collaboration. La perspective de la victoire finale n'empêche pas les équipes de s'entraider pendant l'année dans l'optique de progrès communs.

Les voitures autonomes 1/10ème sont un formidable support pour l'expérimentation concrète de l'intelligence artificielle. Apprentissage par renforcement, apprentissage supervisé, par imitation, apprentissage non supervisé, toute l'IA a rendez-vous à Saclay en avril.

N'hésitez pas à rejoindre la compétition.

logo course de voitures autonomes

## Date de l'édition 2027

L'édition 2027 aura lieu le samedi 3 avril à l'ENS Paris Saclay.

## Editions précédentes

Des résumés et des vidéos des éditions précédentes, ainsi que des guides pour démarrer (premiers programmes python, prise en main du simulateur, apprentissage par renforcement, ROS2...) sont disponibles sur le site de Culture Sciences de l'Ingénieur : [Dossier CoVAPSy Culture Sciences de l'ingénieur](https://sti.eduscol.education.fr/si-ens-paris-saclay/ressources_pedagogiques/dossier-course-de-voitures-autonomes)

photo de la course 2025

## Git

Le [dépôt Git](https://github.com/ajuton-ens/CourseVoituresAutonomesSaclay) permet de trouver le réglement, quelques photos et vidéos, une bibliographie ainsi que l'ensemble des ressources pour participer à la course de voitures autonomes de Paris Saclay et d'y partager les siennes.

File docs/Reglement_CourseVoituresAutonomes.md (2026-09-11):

# Règlement de la Course de Voitures Autonomes de Paris Saclay CoVAPSy

Ce règlement évolue d'année en année, n'hésitez pas à envoyer vos remarques et propositions.

## Le véhicule

Le véhicule doit utiliser un kit châssis/moteur Tamiya TT02 et pour la propulsion une batterie NiMH 7,2V 5000 mAh maximum. Une batterie secondaire, peu importe le type, est autorisée pour alimenter l'électronique. Une alimentation du moteur avec une tension supérieure à la tension batterie n’est pas autorisée. La voiture doit avoir une carrosserie la recouvrant à plus de 80 % (valeur estimée par le jury de manière peu scientifique...).
Le véhicule avec l’ensemble de ses capteurs et actionneurs doit entrer dans les dimensions ci-dessous :

schema dimensions voitures

La voiture doit être visible des véhicules qui la suivent : la voiture doit présenter à l’arrière au moins un rectangle plein de largeur 150 mm et de hauteur 110 mm. Seul un peu de vide (< 10 mm de haut), pour la garde au sol du véhicule est accepté.
Les carrosseries transparentes ou de couleur principale verte, rouge ou grise ne sont pas autorisées. Des guides pour peindre la voiture sont disponibles sur Youtube (ex : https://www.youtube.com/watch?v=MO5J6AqEpbs). Un test avec un lidar RP-Lidar A2M12 ou A2M8 valide la visibilité de l'arrière de la voiture. En cas de non détection (certaines peintures noires absorbent les infra-rouges), du scotch blanc cassé sera ajouté sur l'arrière de la voiture.

Il est possible de supprimer l'entraînement des roues avant au profit du rayon de braquage et au dépend de la motricité.

La voiture doit pouvoir fonctionner en marche avant et en marche arrière.

Pour améliorer la mécanique de la direction, il est possible de changer quelques pièces plastiques par les jeux de pièces en alu du commerce (Yeah Racing TATT-S03BU disponible notamment chez Rcmart.com ou kit Tamiya 54574 vendu chez Conrad).
Toute modification importante du châssis (au-delà de quelques perçages) doit faire l’objet d’une demande et d’une acceptation par les autres établissements participant à la course. L’envoi doit comprendre les références ou plans des modifications prévues.

La communication de l’équipe avec le véhicule doit se limiter à l’envoi d’un signal de démarrage et d’un signal d’arrêt. Le véhicule peut envoyer des informations à l’équipe (télémétrie). Envoyer des commandes modifiant le comportement du véhicule entraîne la disqualification de l’équipe. Pour l'édition 2026, il est autorisé d'utiliser un ordinateur en bord de piste à la fin de calcul déporté. Evidemment, les équipes ne peuvent toucher à cet ordinateur une fois le départ annoncé.

Une voiture type est proposée en kit (voir menu *Voiture type*) par la ménagerie technologique.

## La piste

La forme de la piste n’est pas connue avant le jour de la compétition. Donner des informations sur la forme de la piste à la voiture est interdit. Les arbitres peuvent demander de vérifier ce point sur une piste annexe par exemple. La voiture peut apprendre la piste en faisant jusqu'à 3 tours de mise en place.

La piste est constituée de bordures de 200 mm de hauteur, vertes sur la droite dans le sens du déplacement et rouges sur la gauche dans un sens et inversement dans le sens contraire. Ces bordures sont composées d'éléments droits et d'arcs de cercles de rayon de courbure R = 400mm ou plus. Le sol est un linoléum de couleur grise. La piste est en tout point d’une largeur supérieure à 700 mm, mais peut contenir des obstacles à l'intérieur.

Référence des couleurs : 

* VERT : RAL 6024
* ROUGE : RAL 3020
* SOL : Sol PVC GERFLOR effet béton leone anthracite l.4 m  Réf 83309786 (Leroy Merlin)

Les références des couleurs sont approximatives et les bords de piste parfois marquées par les chocs.

Voici comme exemple une des pistes 2023 :

exemple de trace de piste

Une piste est proposée en kit par la ménagerie technologique.

## Homologations

L’homologation se fait en 4 étapes :

* validation des éléments du véhicule (dimensions, batterie, châssis, couleur détectable par un lidar...),
* validation du démarrage et de l'arrêt à distance, 
* vérification de l’aptitude du véhicule à se déplacer sur un élément droit de piste plus un virage sans toucher les bordures,
* vérification de l’aptitude du véhicule à repartir en marche arrière en cas de blocage contre un obstacle et en l'absence de véhicule derrière,
* vérification de l'aptitude du véhicule à éviter un obstacle de la taille d'une voiture sur un tronçon de piste.

L'ensemble des arbitres peut envisager une homologation avec pénalité pour de légères infractions au règlement : un véhicule qui ne s'arrête pas ou mal à distance, non fonctionnement de la marche arrière par exemple.

Pour les courses comme pour les qualifications, une voiture faisant du SLAM peut faire jusqu'à 3 tours de mise en place, sans obstacles. Les obstacles ou les voitures adverses sont ajoutées après, une fois la voiture en place sur la grille de départ.

## Qualifications 1 - contre la montre

La première phase de qualification se déroule sur 2 passages avec une voiture seule sur une piste A comportant des obstacles fixes d'une taille proche de celle d'une voiture.
A chaque passage, la voiture s’élance pour 2 tours. Le meilleur des 2 temps est retenu, afin de palier à un éventuel problème technique survenu lors du premier passage. Un des passages se fait dans le sens horaire et le second dans le sens trigonométrique.

En cas d'échec sur les 2 passages à terminer les 2 tours, un temps de 120 s est retenu si la voiture a fait un tour, 180 s si elle n'a pas même fini un tour.

A l'issue de la première phase de qualification, la première voiture obtient 25 points, la seconde 24 points et ainsi de suite jusqu'à 5 points minimum pour toute voiture ayant moins de 120 s. Une voiture ayant effectué juste un tour (temps de 120s) obtient un point.

## Qualifications 2 - courses

La seconde phase de qualification se fait lors de 2 courses de poules regroupant 4 à 8 voitures sur 3 tours d'une piste B et 3 tours d'une piste C (une dans le sens horaire et l'autre dans le sens trigonométrique). La manière d'établir les N poules est établie en fonction du classement des qualifications (la poule n est composée des voitures classées n%N, n étant le numéro de la poule et N le nombre de poules). A chaque course la voiture accumule des points pour le classement général des qualifications : 10 points pour le premier, 8 points pour le 2nd, 6 pour le 3ème, 4 pour les voitures ayant bouclé les 3 tours et 1 point pour les voitures n'ayant pas terminé la course.

Pour chaque course (y compris la course finale) : 

* Les équipes ont 3 min pour installer leur véhicule sur la piste.
* L’ensemble des véhicules de la poule est positionné sur la grille de départ selon les résultats des qualifications.
* Une fois que toutes les équipes ont annoncé être prêtes, il est interdit de toucher les véhicules. Le signal de départ est donné oralement par l’arbitre.
* L’ordre d’arrivée est relevé après un nombre de tours définis à l’avance (3 par défaut pour la phase de qualification et 5 pour les phases finales).
* Une voiture ne terminant pas le nombre de tours définis n'est pas classée.

L'arbitre et les commissaires de course veillent au bon déroulement des courses :

* Un véhicule ayant un comportement notoirement agressif envers les véhicules adverses est disqualifié retiré de la piste, de même qu'une voiture empêchant volontairement une autre de la doubler.
* un véhicule immobilisé sur la piste plus de 10 secondes en l'absence d'une voiture le bloquant est retiré de la piste.
* un véhicule ayant parcouru plus de 2 m à contre-sens est retiré de la piste.

## Les phases finales - courses, en 2 manches

A l'issue des qualifications, chaque voiture obtient 2 scores : 

* le total coursesQualif (la somme des points obtenus lors des 2 courses de qualification)
* le total CLM+courseQualif(le score précédent plus les points obtenus en qualification contre la montre).

2 manches sont composées de chacune de 3 courses.

Les 2 premiers de chaque poule (avec le score courseQualif, le score CLM+courseQualif servant à départager les ex-aequo) font les courses 1 de chaque manche, les 3ème et 4ème font les courses 2 de chaque manche et les autres font la course 3 de chaque manche. Le classement des qualifications (avec le score courseQualif, le score CLM+courseQualif servant à départager les ex-aequo) détermine la grille de départ, la voiture ayant le plus de points s’élançant en tête sur la grille de départ. 

Les arbitres relèvent l’ordre d’arrivée après un nombre de tours définis à l’avance (5 par défaut) et attribuent les points de la manière suivante : 25 pts pour le 1er, 18 pts pour le 2e, 15 pts pour le 3e, 12 pts pour le 4e ; 10 pts pour le 5e, 8 pts pour le 6e ; 6 pts pour le 7e, 4 pts pour le 8e ; 2 pts pour le 9e et 1 pt pour le 10e. Une voiture ne terminant pas le nombre de tours défini obtient 0 point. Une fois les voitures de la première course classées, on continue l'attribution des points aux voitures de la 2nde course. 

Le classement final se fait avec les points des 2 courses finales uniquement. En cas d'égalité, le score CLM+courseQualif est pris en compte pour le classement final. Si il y a de nouveau égalité, le score coursesQualif départage les équipes.

Les prix récompensent les 1er, 2ème, 3ème du classement général. S'y ajoute un prix de l'innovation et un prix pour les 1ers parmi les licences.

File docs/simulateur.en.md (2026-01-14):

# Simulator for the Paris-Saclay Autonomous Car Race

To accelerate the development of algorithms for autonomous cars, several teams use the Webots R2025a simulator.

For the 2025-2026 season, a Webots R2025a project with a standard car, a basic controller in C, one in Python, and elements from the official track is available on GitHub, in the archive [Simulateur_CoVAPSy_Webots2025a](https://github.com/ajuton-ens/CourseVoituresAutonomesSaclay/blob/main/Simulator/Simulateur_CoVAPSy_Webots2025a_Base.zip)

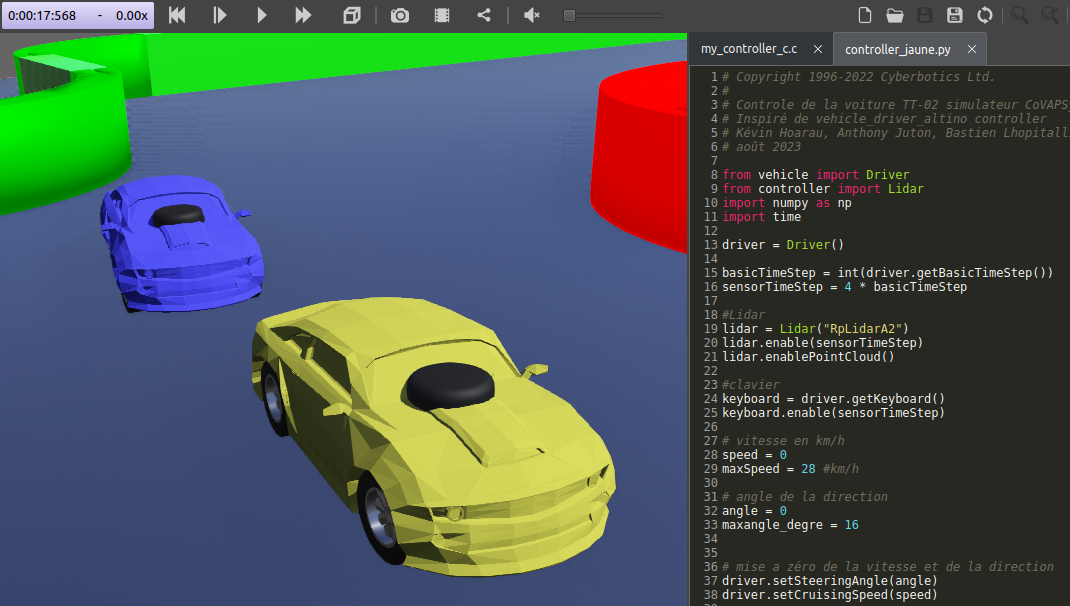
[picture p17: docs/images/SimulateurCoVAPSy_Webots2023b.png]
Webots screenshot


A pedagogical article to get started is available on Culture Sciences de l'Ingénieur: [CoVAPSy, implementation of the Webots simulator](https://sti.eduscol.education.fr/si-ens-paris-saclay/ressources_pedagogiques/covapsy-mise-en-oeuvre-du-simulateur-webots)

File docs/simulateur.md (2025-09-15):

# Simulateur pour la course de voitures autonomes de Paris Saclay

Pour accélérer le développement d'algorithmes pour les voitures autonomes, plusieurs équipes utilisent le simulateur Webots R2025a.

Pour la saison 2025-2026, un projet webots R2025a avec une voiture type, un contrôleur basique en C et un en python et des éléments de la piste officielle est disponible sur le git, dans l'archive [Simulateur_CoVAPSy_Webots2025a](https://github.com/ajuton-ens/CourseVoituresAutonomesSaclay/blob/main/Simulator/Simulateur_CoVAPSy_Webots2025a_Base.zip)

copie d'écran Webots

Sur Culture Science de l'ingénieur se trouve un article pédagogique pour démarrer : [CoVAPSy, mise en oeuvre du simulateur webots](https://sti.eduscol.education.fr/si-ens-paris-saclay/ressources_pedagogiques/covapsy-mise-en-oeuvre-du-simulateur-webots)

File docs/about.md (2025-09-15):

Course de Voitures Autonomes Paris Saclay CoVAPSy

Contact : anthony.juton@ens-paris-saclay.fr

Le logo a été créé avec le logiciel DALL-E de openai.

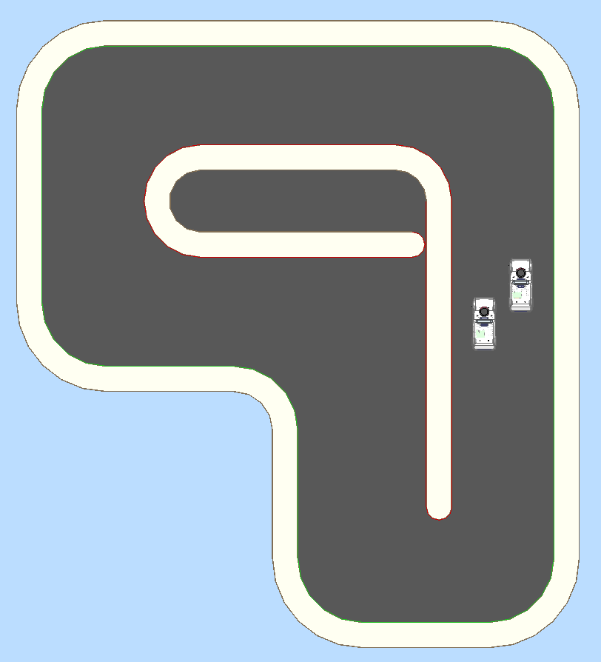
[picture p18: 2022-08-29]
Hardware/images_modélisation_3D/Capture piste.PNG

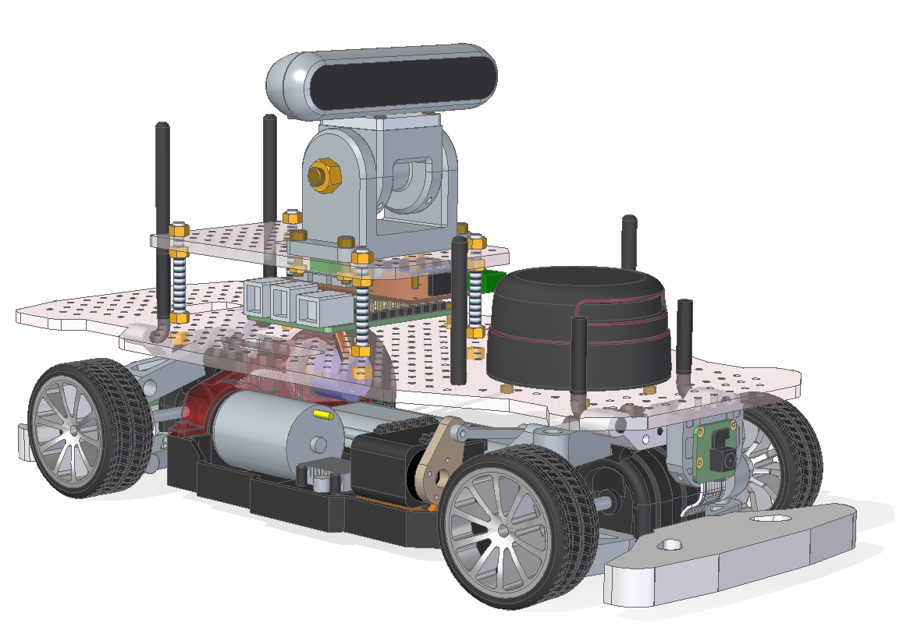
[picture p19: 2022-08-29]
Hardware/images_modélisation_3D/profil avant gauche.PNG

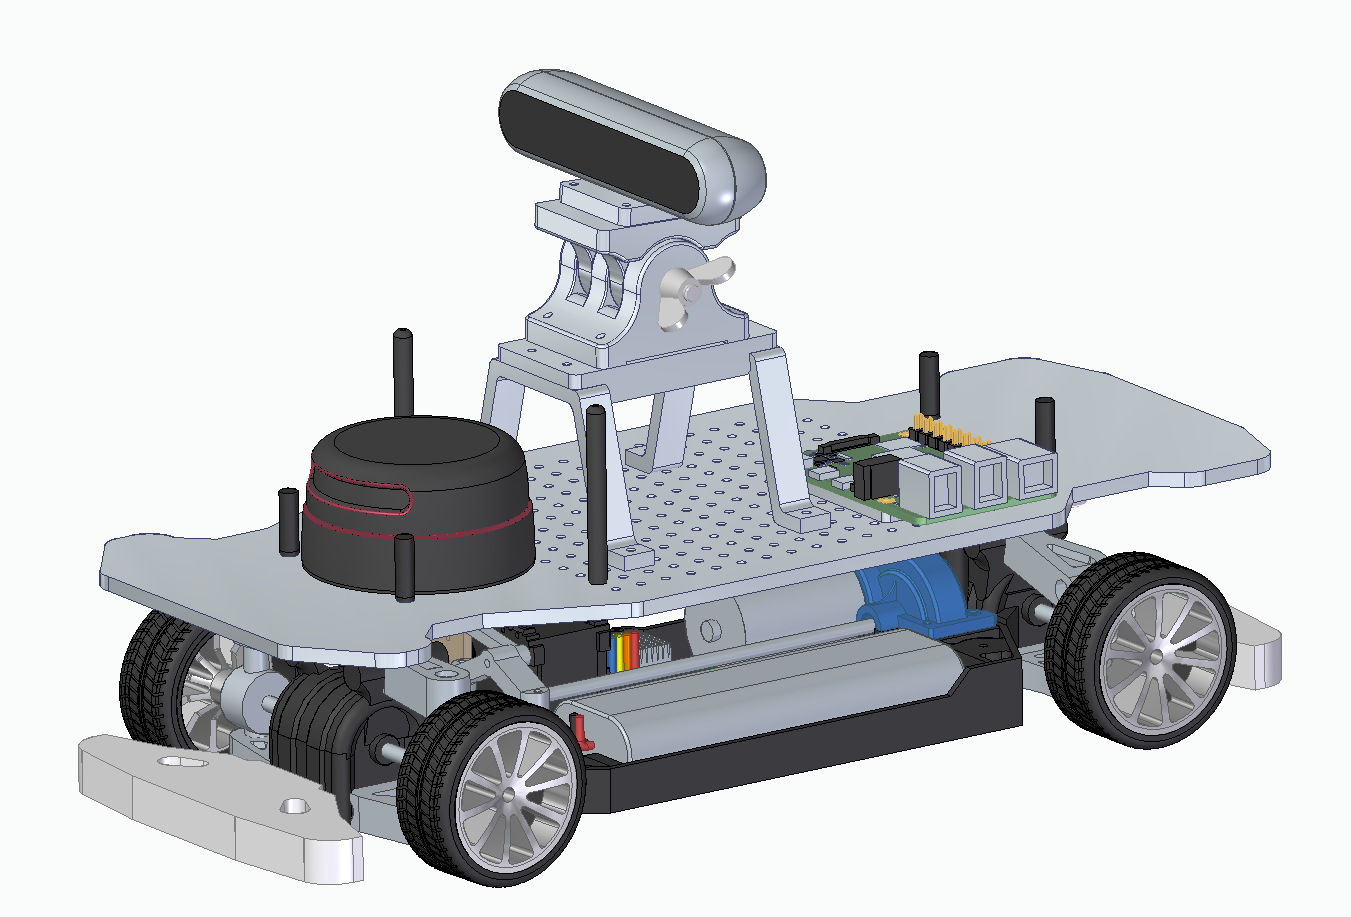
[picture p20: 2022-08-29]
Hardware/images_modélisation_3D/Capture vehicule.PNG

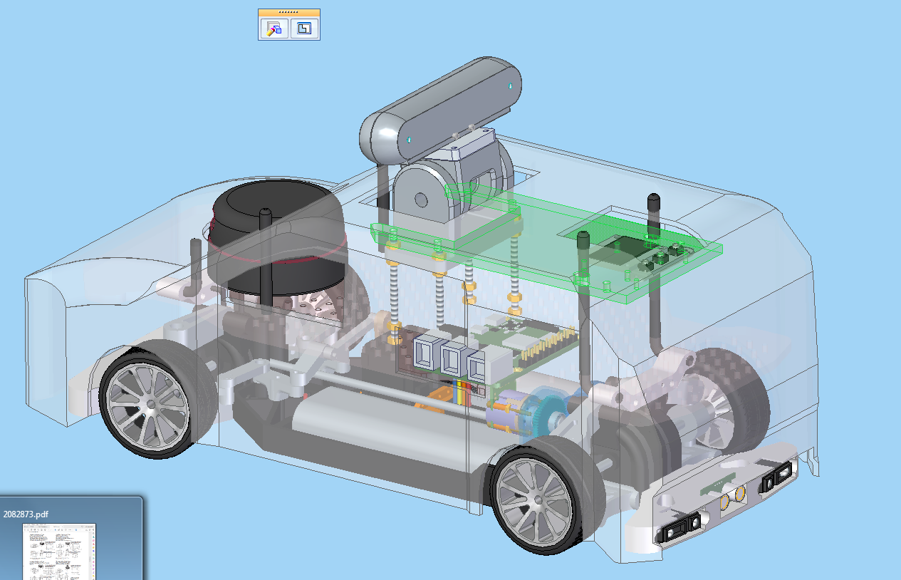
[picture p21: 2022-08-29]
Hardware/images_modélisation_3D/Capture2.PNG

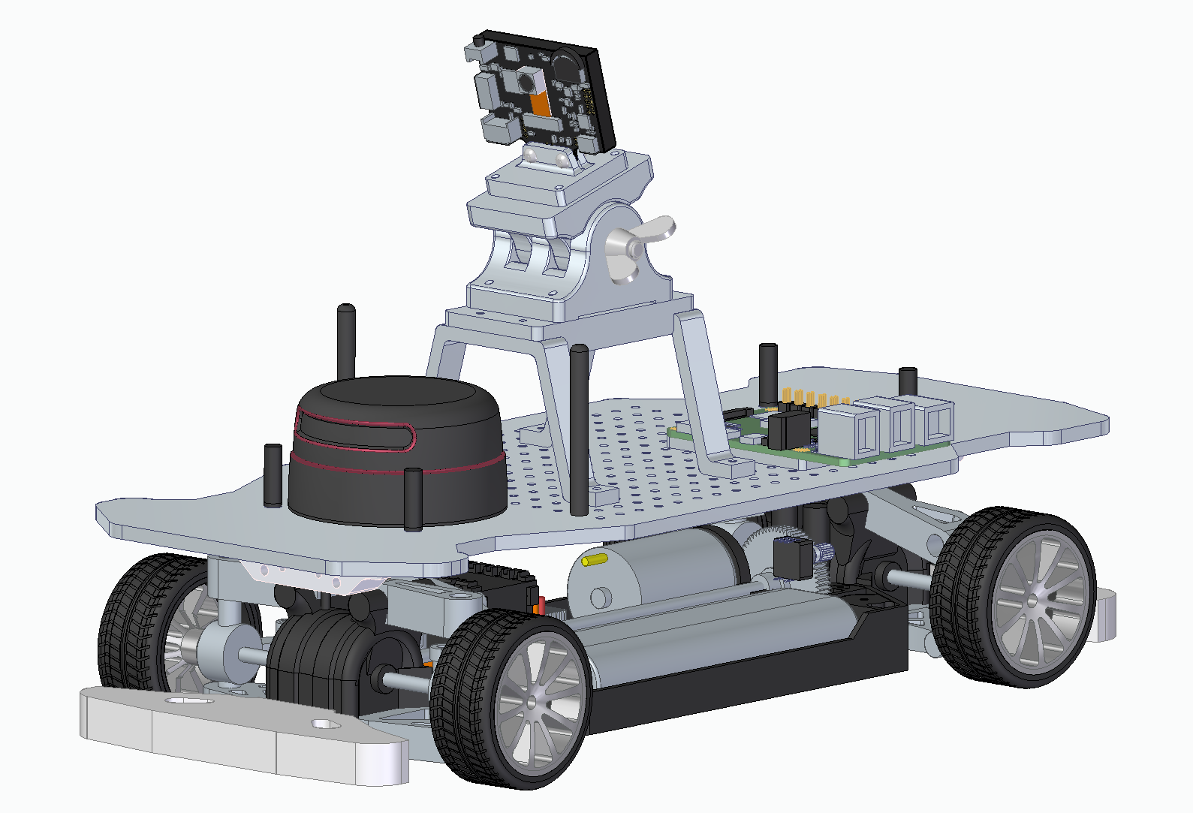
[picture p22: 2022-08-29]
Hardware/images_modélisation_3D/Captures Camera Huskylens incliné.PNG

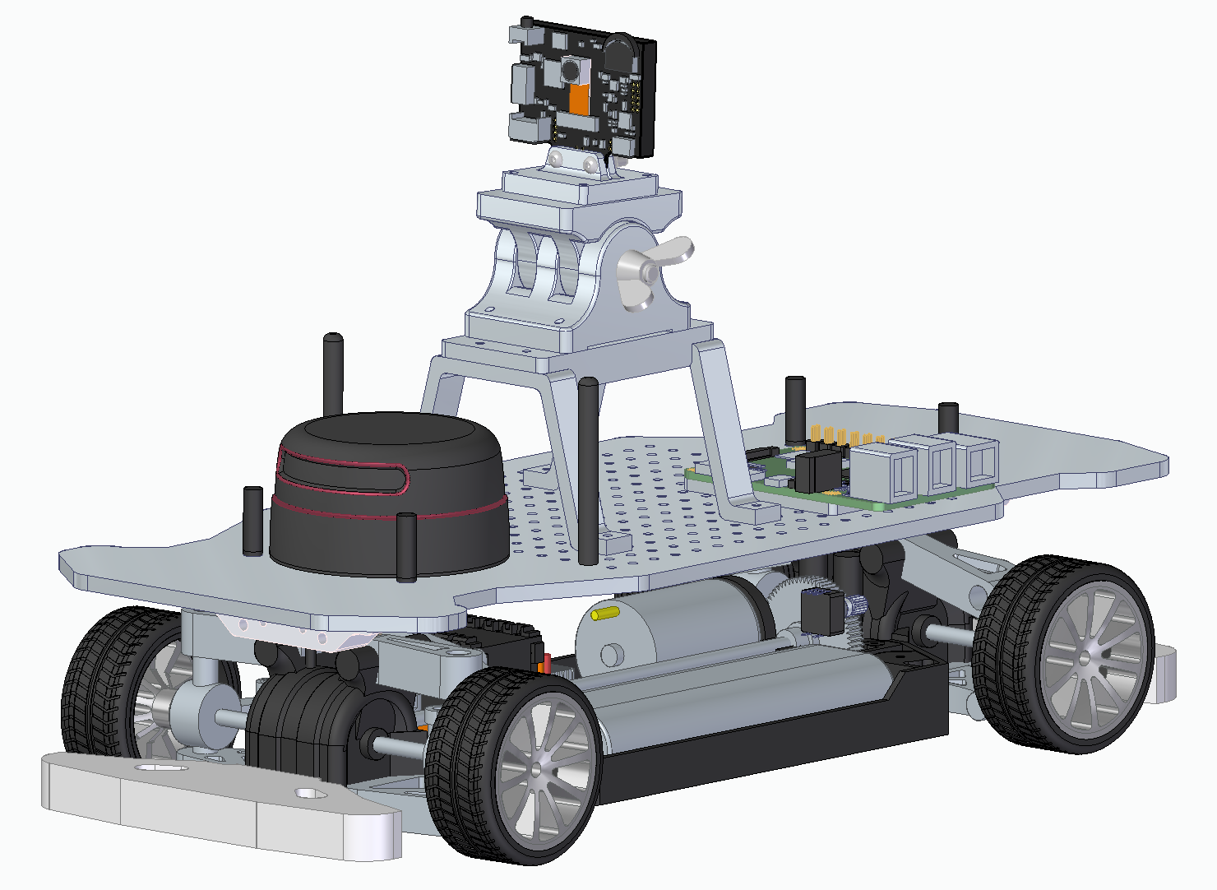
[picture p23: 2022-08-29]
Hardware/images_modélisation_3D/Captures Camera Huskylens.PNG

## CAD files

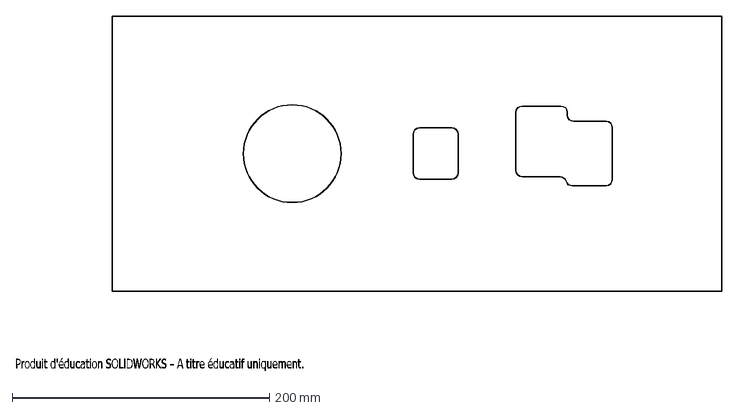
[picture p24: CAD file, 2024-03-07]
Hardware/pieces_mecaniques_stp_dxf/Gabarit de découpe voiture.DXF
Produit d'éducation SOLIDWORKS – A titre éducatif uniquement.

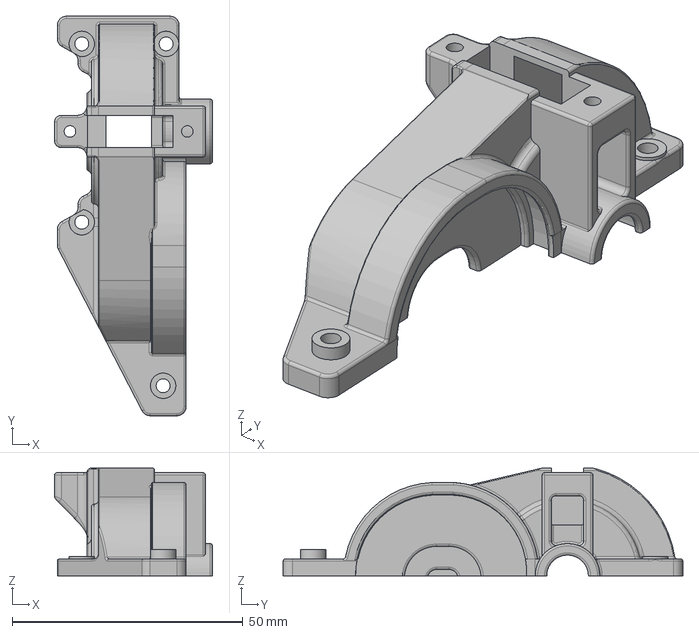
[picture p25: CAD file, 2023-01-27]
Hardware/pieces_mecaniques_stp_dxf/Carter pignon support fourche.stp
34.2 x 86.5 x 23.3 mm

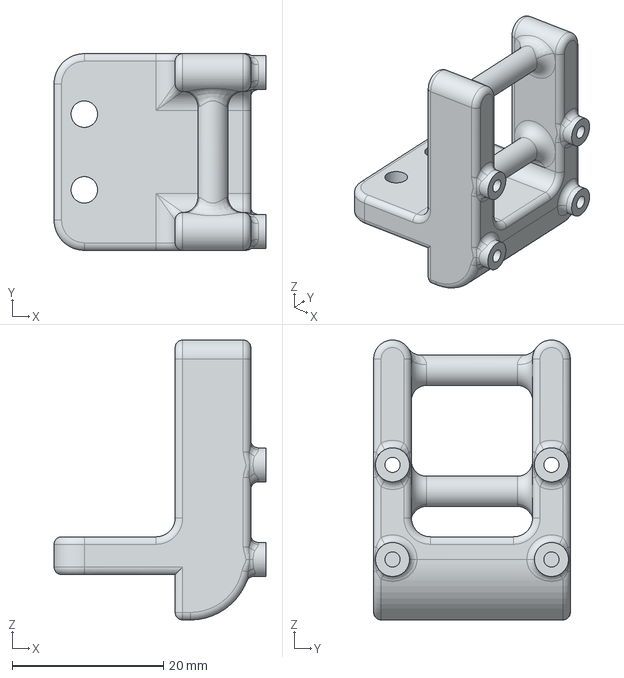
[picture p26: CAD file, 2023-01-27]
Hardware/pieces_mecaniques_stp_dxf/Support caméra avant .stp
28.0 x 26.0 x 37.0 mm

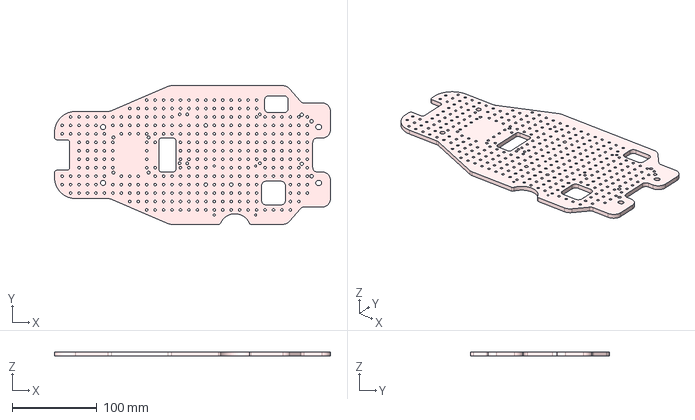
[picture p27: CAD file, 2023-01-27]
Hardware/pieces_mecaniques_stp_dxf/Plaque trouée.stp
326.5 x 164.0 x 5.00 mm

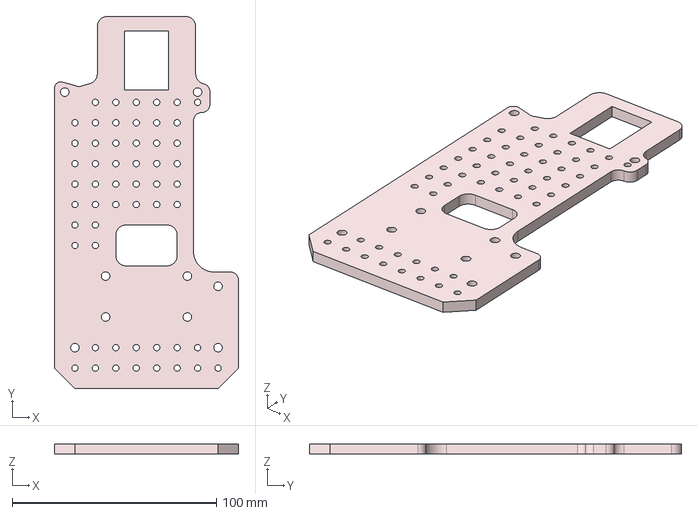
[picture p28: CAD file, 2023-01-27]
Hardware/pieces_mecaniques_stp_dxf/Plaque trouée supérieure.stp
90.0 x 182.0 x 5.00 mm

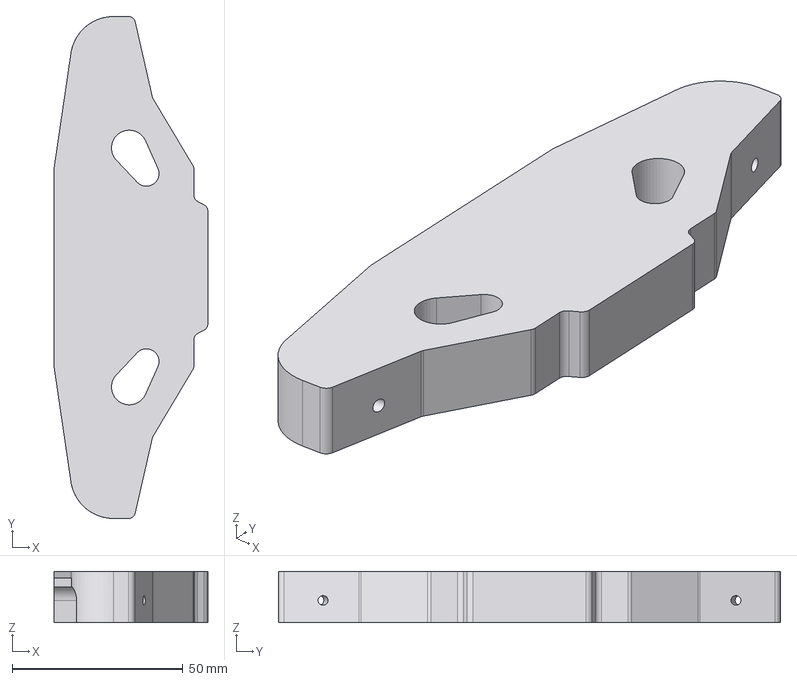
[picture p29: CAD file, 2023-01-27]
Hardware/pieces_mecaniques_stp_dxf/Pare-choc arrière.stp
45.0 x 147.0 x 15.0 mm

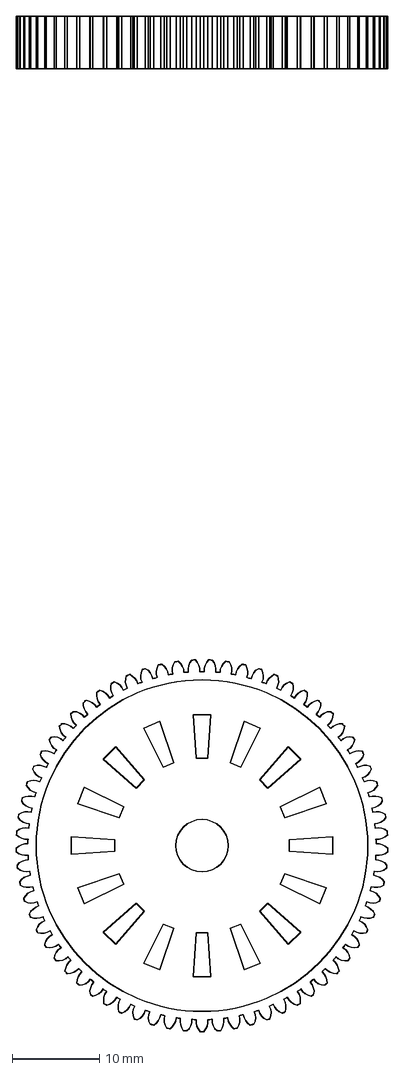
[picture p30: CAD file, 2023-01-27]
Hardware/pieces_mecaniques_stp_dxf/Pignon intermediaire 70dts.dxf
42.6 x 116.3 mm

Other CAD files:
Hardware/pieces_mecaniques_stp_dxf/Plaque trouée supérieure.dxf
Hardware/pieces_mecaniques_stp_dxf/Plaque trouée.dxf

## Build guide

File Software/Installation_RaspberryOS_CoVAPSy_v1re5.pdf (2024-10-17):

# Installation de Raspberry OS sur Raspberry Pi 4

## CoVAPSy : Premiers programmes python sur la voiture réelle

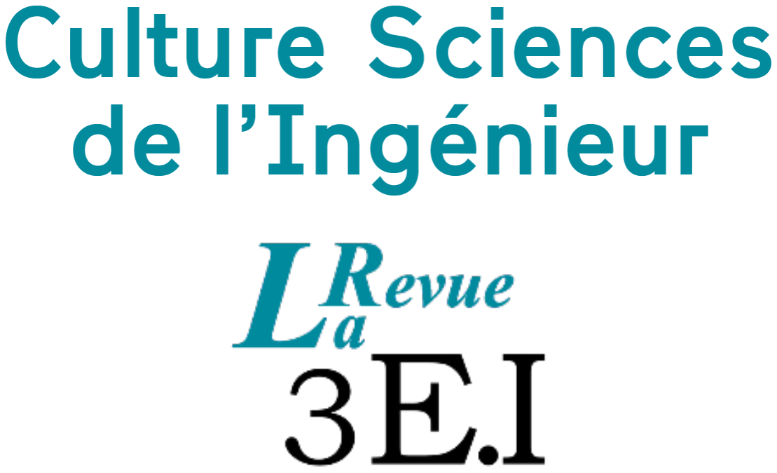
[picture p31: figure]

Anthony JUTON¹ | Version 1.5 du 17/10/24

Cette ressource est une annexe à la ressource « CoVAPSy : Premiers programmes python sur la

voiture réelle » [1] et fait partie du N°111 de La Revue 3EI de janvier 2024. Cette annexe est

mise à jour au moment de sa publication, les mises à jour ultérieures sont disponibles sur [2].

Le nano-ordinateur Raspberry Pi 4 peut être utilisé comme un PC avec écran et clavier. Il est utilisé ici comme un serveur « Headless », c’est à dire sans écran ni clavier. On y accède par un bureau virtuel ou par une console depuis un PC personnel. Ce document présente l’installation de Raspberry OS et les outils nécessaires pour un accès au nano-ordinateur, sans écran ni clavier.

Les informations concernant la carte Raspberry Pi 4 sont disponibles sur le site de Raspberry : https://www.raspberrypi.com/products/raspberry-pi-4-model-b/

## 1 - Installation de l’OS

1.1 - Création de l’image

Le site Raspberry explique en détail comment installer le système d’exploitation sur la PI 4.

Pour installer Raspberry OS sur la carte, on crée une image du système d’exploitation sur la carte SD du nano-ordinateur via un PC personnel.

Pour créer cette image, on insère la carte SD dans le PC et on commence par télécharger Raspberry Pi Imager : https://www.raspberrypi.com/software/

On choisit Raspberry OS 64bits et la carte SD.

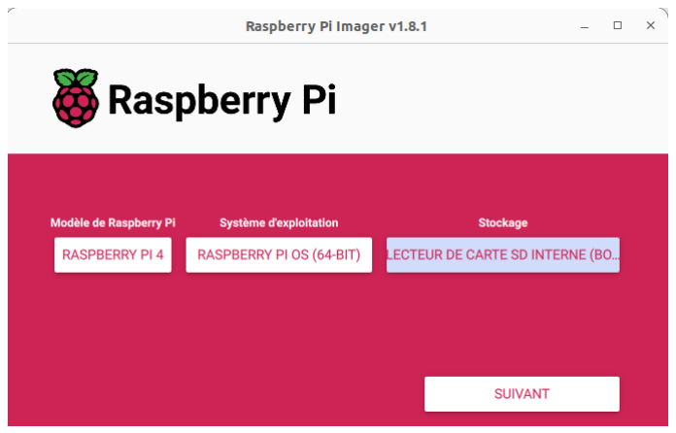
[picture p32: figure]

Figure 1: Fenêtre du logiciel Raspberry

Imager avant écriture de la carte SD

Le bouton Suivant puis l’option Modifier les réglages permettent d’ajouter une configuration de

connexion au réseau WIFI (ce peut être un point d’accès WIFI créé par un smartphone) en

indiquant un nom de réseau Wifi (SSID) et la clé WPA associée (password). Activer également SSH

(pour un accès à distance)

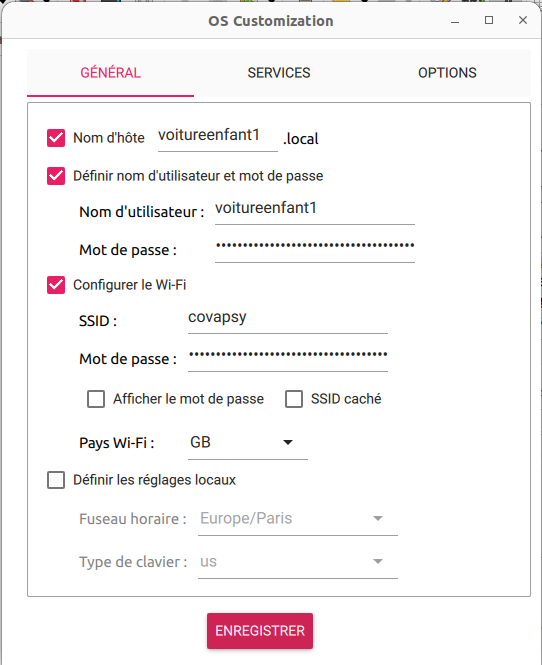
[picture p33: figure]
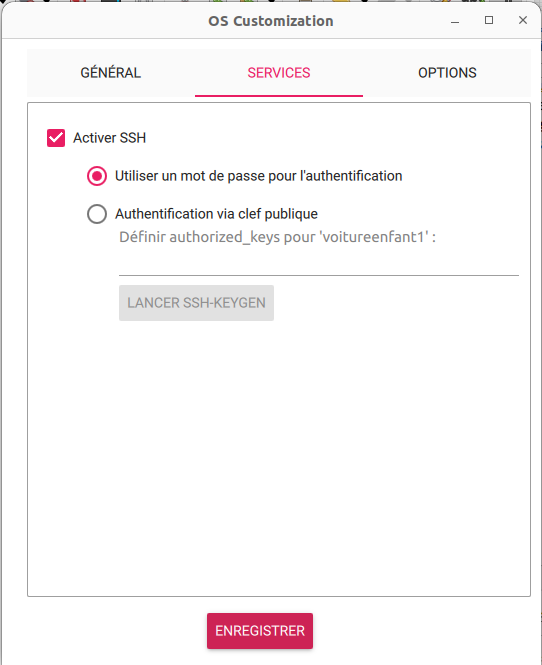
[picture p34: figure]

Figure 2 : Paramètres de l'image Raspberry OS

Attention, le nano-ordinateur se trouvant connecté à Internet, il est nécessaire de ne surtout pas laisser le login pi associé au mot de passe raspberry.

La configuration est terminée. Cliquer sur Enregistrer puis Yes à la demande d’appliquer les modifications. Générer la carte (bouton Ecrire) et l’insérer dans la raspberry pi.

1.2 - Recherche de l’IP du nano-ordinateur

Une fois ces configurations effectuées, le nano-ordinateur démarre, connecté soit sur le WIFI si il a été configuré lors de la préparation de la carte SD, soit branché par un câble Ethernet à un routeur apte à lui donner une adresse IP (la box de la maison ou un routeur du commerce). Pour s’y connecter à distance, il est alors nécessaire d’avoir son adresse IP, adresse notée sous la forme de 4 nombres 192.168.1.4 par exemple (en IPv4).

Le PC doit être bien évidemment connecté sur le même réseau local.

- Il est possible de connecter un écran sur le port micro-hdmi et un clavier et une souris. Cette solution demandant du matériel supplémentaire et peu ergonomique pour la suite, ce document se concentre sur les solutions headless.
- Une solution simple est de faire un ping avec une recherche DNS locale, depuis une console (nommée invite de commande sous windows) avec le hostname défini dans la partie précédente, par exemple : ping voitureenfant1.local

Le nano-ordinateur répond alors avec son adresse IP.

Figure 3 : Réponse à une recherche DNS locale

Parfois, notamment sous Windows, le DNS local ne fonctionne pas.

- Si le nano-ordinateur est connecté sur un réseau Ethernet filaire ou wifi avec un serveur DHCP (c’est-à-dire qu’une machine, le routeur ou la box habituellement sur les petits réseaux, distribue les adresses IP), on peut y trouver l’adresse IP du nano-ordinateur. Pour cela, on se rend sur la page web de la box ou du routeur (la page web de la box internet pour une utilisation à domicile, souvent accessible à l’adresse 192.168.1.1).

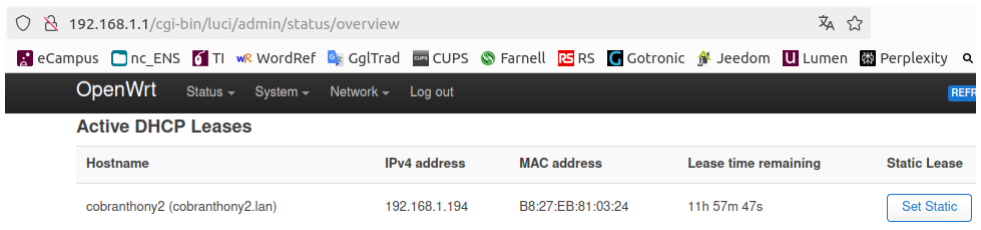
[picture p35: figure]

Figure 4: Page d'accueil du routeur OpenWRT avec une carte raspebrry pi de

connectée. Le bouton "Set static" permet de réserver l'adresse.

On présente ici les pages d’une LiveBox. Les routeurs grand public et les box ont la même apparence avec une vue globale (overview) du réseau local où on trouve les IP des équipements connectés et des pages de configuration avancée (parfois nommées LAN network), notamment pour la réservation des adresses IP.

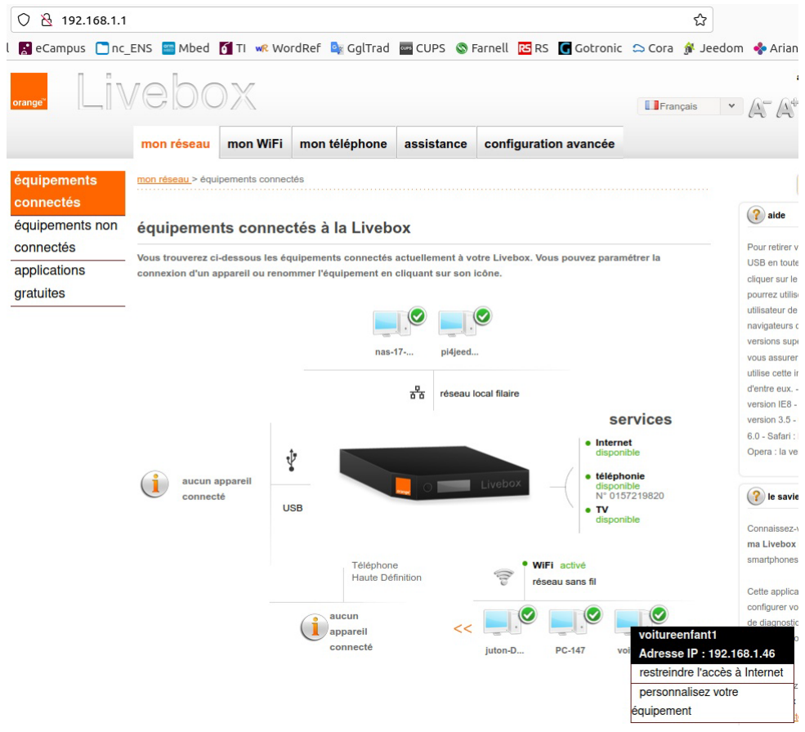
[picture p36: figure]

Figure 5: Présentation des équipements connectés au réseau par une LiveBox

Il est alors possible de réserver l’adresse IP dans le serveur DHCP, de sorte que le nano-ordinateur obtienne toujours la même adresse lors de ces nouvelles connexions.

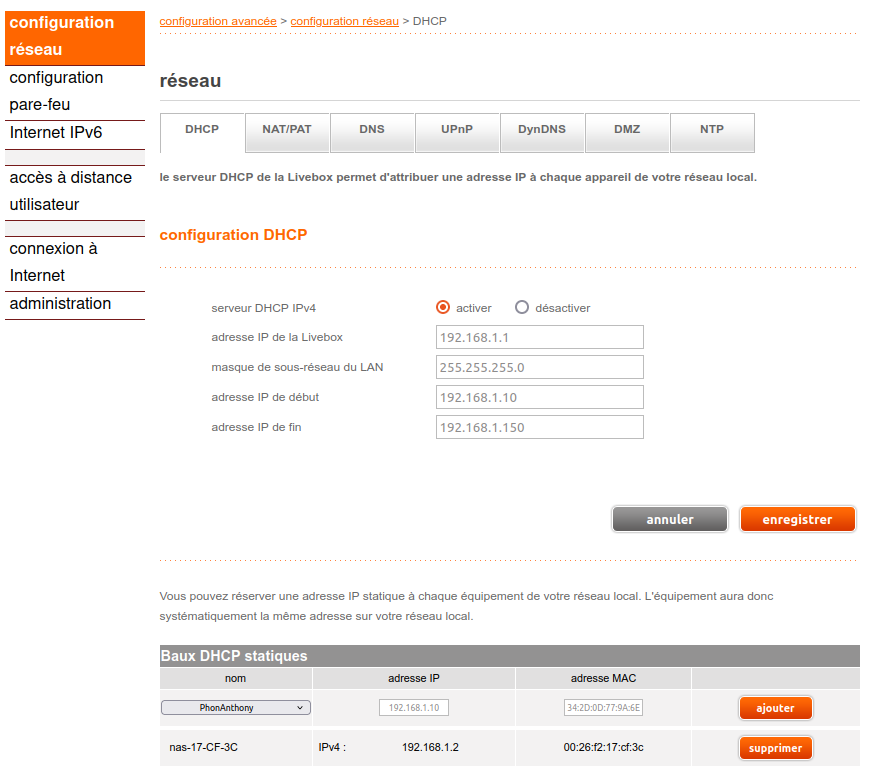
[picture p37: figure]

Figure 6 : Page de configuration DHCP d’une livebox où sont attribuées les adresses IP statiques (ou IP réservées)

1.3 - Connexion SSH

Une fois l’IP découverte, il est aisé de se connecter en SSH (Secure Shell). SSH est un protocole de communication sécurisé permettant de dialoguer via une console du serveur SSH ouverte sur le client SSH. Le nano-ordinateur est serveur SSH et le PC utilisateur est client SSH.

Très utile pour les accès à distance, le serveur SSH est installé par défaut sur les Raspberry Pi (et il a été activé dans les options lors de la création de la carte SD).

Le client SSH est installé sur les PC Linux (et sans doute Mac) et parfois sur Windows. Si cela n’est pas le cas sur Windows, on peut installer Putty par exemple.

Depuis une console (terminal Linux, invite de commande Windows ou Putty), on tape :

ssh login@<adresse IP de la raspberry pi>

L’authenticité de ce serveur SSH n’étant pas attesté, une demande de confirmation attend la réponse yes, lors de la première connexion, puis le mot de passe de l’utilisateur.

Lorsque la connexion est réussie, le prompt indique :

le_nom_de_l_utilisateur@le_nom_de_la_machine, ici voitureenfant1@voitureenfant1

La commande exit permet de couper la connexion.

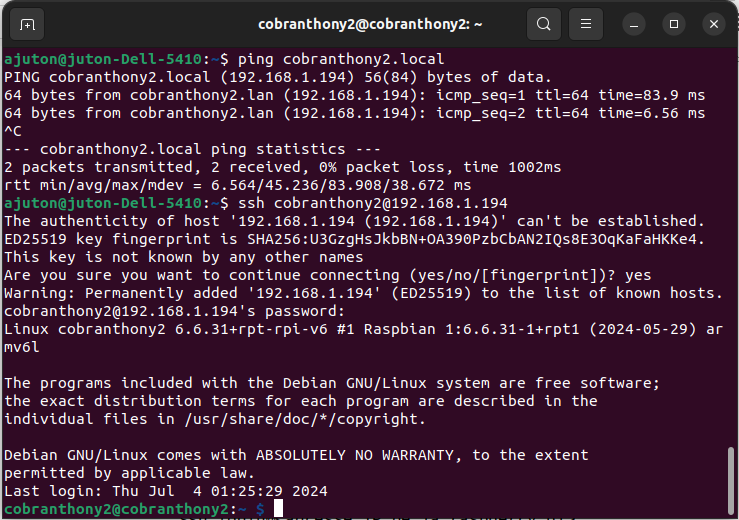
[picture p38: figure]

Figure 7: Connexion ssh à la Raspberry pi depuis un PC relié sur le même

réseau local

Copie de fichiers à distance scp

Il est possible d’utiliser ssh pour transférer des fichiers entre l’ordinateur (PC) et le nano-ordinateur (raspberry pi). La commande s’appelle scp pour ssh copy.

Pour copier un fichier depuis le PC vers le dossier Documents de la raspberry pi. On se place dans le dossier correspondant du PC (sous linux, on clique droit dans le dossier dans l’explorateur de Fichier et on choisit Ouvrir dans un terminal). Sous windows, il est possible de se déplacer dans les dossiers depuis l’invite de commande avec la commande cd (change directory) :

scp nom_du_fichier le_nom_de_l_utilisateur@le_nom_de_la_machine:Documents

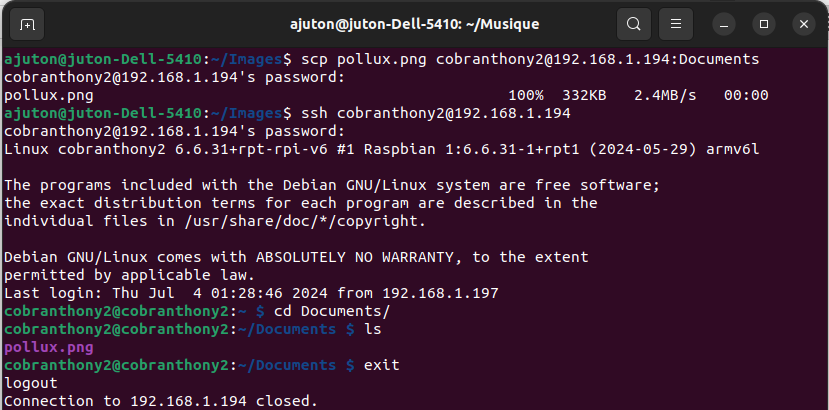
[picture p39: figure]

Figure 8: Console d'une copie de fichier du PC vers la raspberry Pi

Pour copier un fichier depuis le dossier Documents de la raspberry pi vers le PC :

scp le_nom_de_l_utilisateur@le_nom_de_la_machine:Documents/nom_du_fichier .

Le point à la fin permet d’indiquer que le fichier doit être déposé à l’emplacement d’où l’on envoie la commande scp.

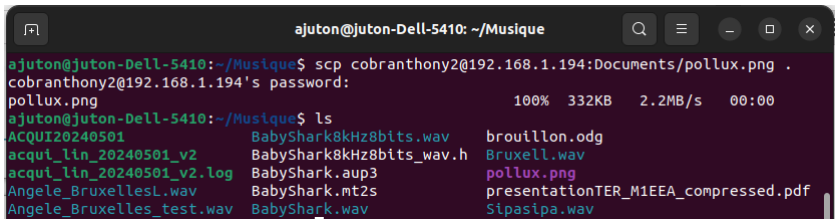
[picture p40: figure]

Figure 9: Copie depuis le PC d'un fichier de la raspberry Pi vers un dossier du PC

## 2 - Bureau à distance

Pour faciliter l’utilisation du nano-ordinateur dans un premier temps, les outils graphiques sont plus accessibles que la ligne de commande. Celui-ci étant gourmand en ressource, il peut être intéressant de le désactiver une fois que la configuration est correcte et qu’il n’y a que du code à écrire.

### 2.1 Mise en œuvre d’un bureau à distance VNC

VNC (Virtual Network Computing) est un protocole de bureau à distance. Le serveur VNC est la Raspberry Pi et le client VNC est le PC utilisateur.

Le site raspberrypi.com propose là encore des solutions :

https://www.raspberrypi.com/documentation/computers/remote-access.html#virtualnetworkcomputing-vnc (https://www.raspberrypi.com/documentation/computers/remote-access.html#virtual-networkcomputing-vnc)

### 2.1.1 Installation du client sur le PC

Raspberry propose la solution gratuite mais propriétaire de RealVNC. Il est possible de télécharger le client vnc (nommé VNC Viewer) : sur le site (https://www.realvnc.com/en/), onglet Download, choisir la version adaptée de VNC Viewer à l’OS de l’ordinateur et l’installer.

### 2.1.2 Activation du serveur VNC sur le nano⁻ordinateur Raspberry Pi

Realvnc-vnc-serveur est installé avec l’image de Raspberry OS. Pour l’activer, utiliser la fenêtre de configuration raspi-config, depuis l’accès SSH :

sudo raspi-config

Ensuite, choisir Interface Options > VNC › Yes.

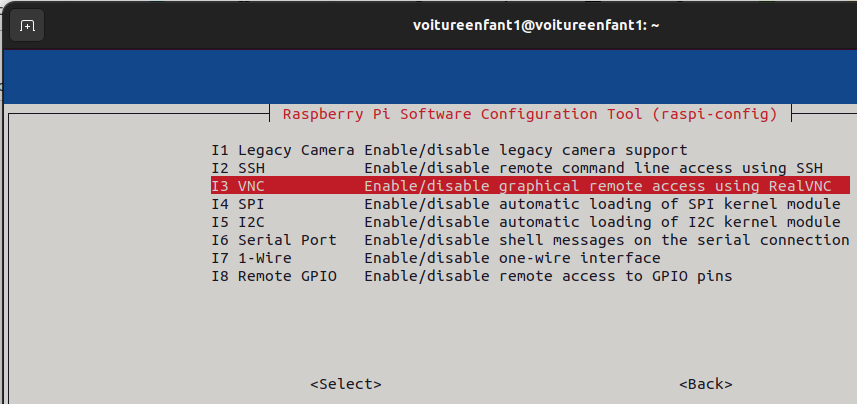
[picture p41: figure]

Figure 10 : Extrait de la fenêtre raspi-config

Enfin, aller sur Ok puis Finish pour fermer raspi-config.

### 2.1.3 Connexion locale au serveur vnc

Pour se connecter en VNC depuis un PC connecté sur le même réseau que le nano-ordinateur, lancer VNC Viewer, indiquer l’adresse IP de la Raspberry Pi, accepter les recommandations de précautions, introduire son login et son mot de passe.

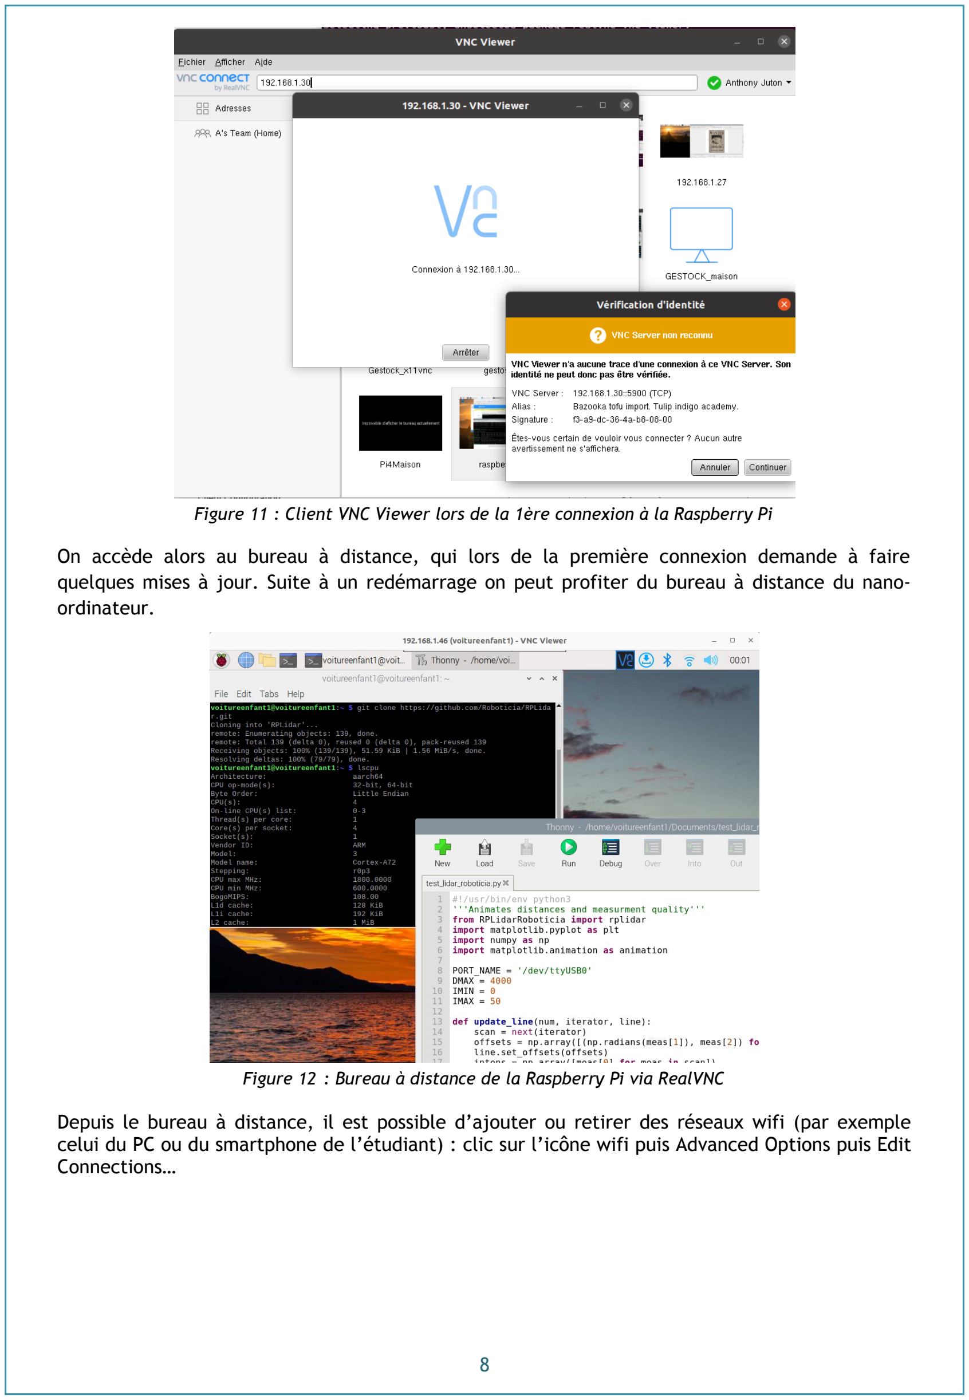
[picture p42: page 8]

Figure 11 : Client VNC Viewer lors de la 1ère connexion à la Raspberry Pi

On accède alors au bureau à distance, qui lors de la première connexion demande à faire quelques mises à jour. Suite à un redémarrage on peut profiter du bureau à distance du nano-ordinateur.

Figure 12 : Bureau à distance de la Raspberry Pi via RealVNC

Depuis le bureau à distance, il est possible d’ajouter ou retirer des réseaux wifi (par exemple celui du PC ou du smartphone de l’étudiant) : clic sur l’icône wifi puis Advanced Options puis Edit Connections…

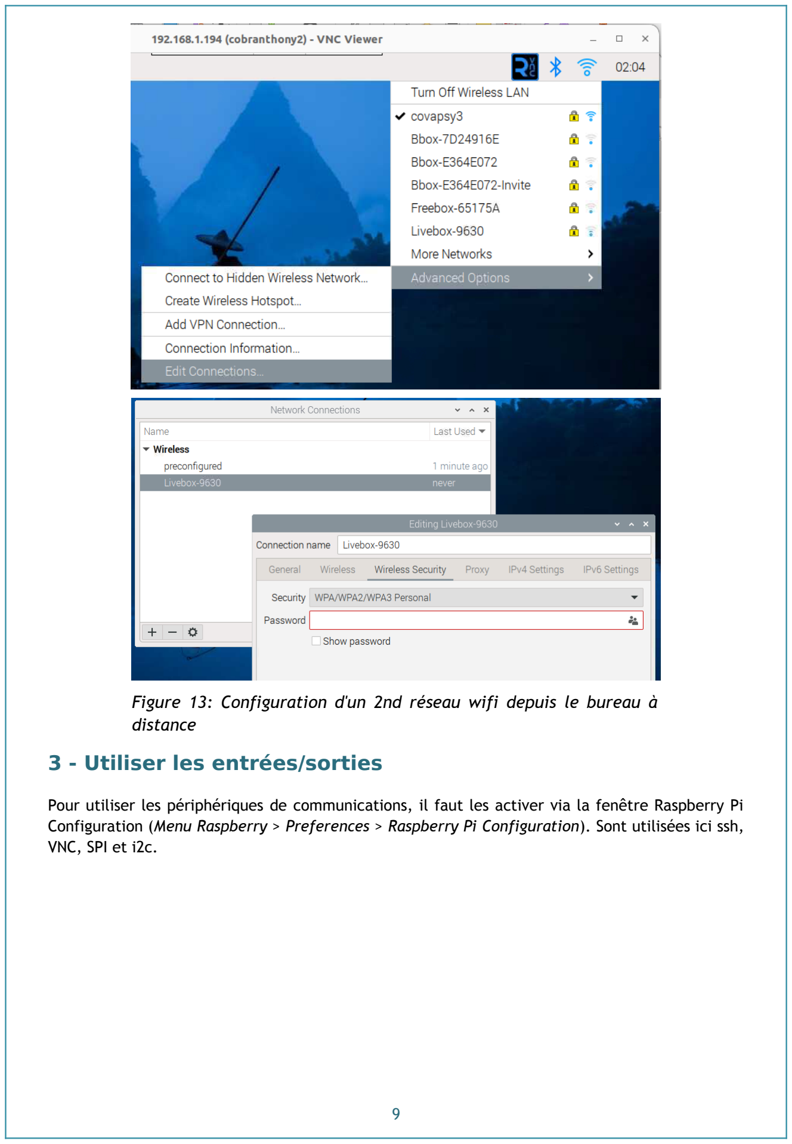
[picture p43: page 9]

Figure 13: Configuration d'un 2nd réseau wifi depuis le bureau à

distance

## 3 - Utiliser les entrées/sorties

Pour utiliser les périphériques de communications, il faut les activer via la fenêtre Raspberry Pi

Configuration (Menu Raspberry > Preferences > Raspberry Pi Configuration). Sont utilisées ici ssh, VNC, SPI et i2c.

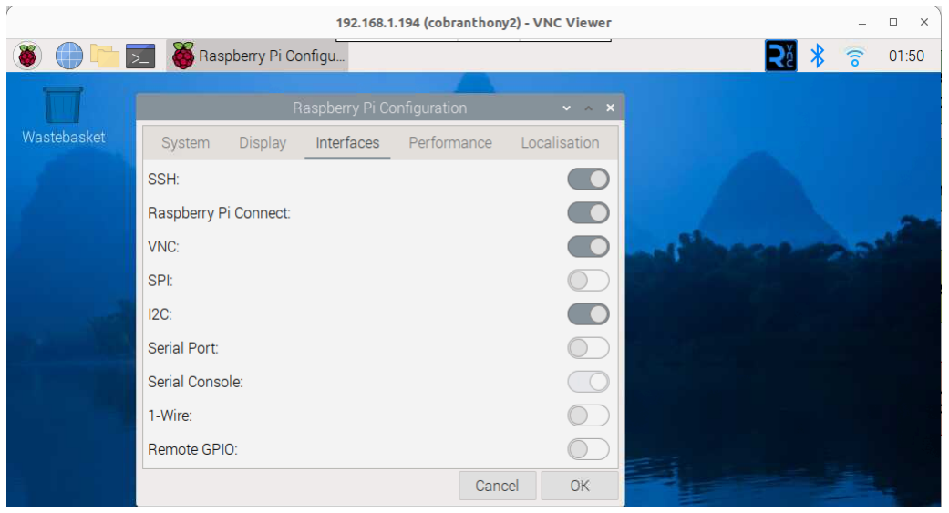
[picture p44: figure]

Figure 14: Activation des bus i2c et SPI via Raspberry Pi Configuration

Plus d’infos sur https://gpiozero.readthedocs.io/en/stable/installing.html

3.1 - Installation des paquets utiles

Pour le bon fonctionnement de la voiture, quelques paquets Linux sont utiles. Ils seront présentés plus loin.

Depuis la console, lancer les commandes d’installation suivantes pour mettre à jour le système et installer la bibliothèque matplotlib et les bibliothèques pour les pwm et le lidar :

sudo apt update && sudo apt upgrade -y
sudo apt install python3-matplotlib -y

pip install rpi-hardware-pwm rplidar-roboticia -⁻break-system-packages

Python demande désormais par défaut d’utiliser des environnements virtuels. La raspberry Pi ne servant qu’à la conduite autonome, on peut installer les modules python hors environnement virtuel, soit en installant le paquet depuis les dépôts linux officiels de la distribution :

sudo apt install python3-nomdumodule
ou

pip install nomdumodule -⁻break-system-packages

3.2 - Les PWM matérielles

Pour la commande des moteurs, on utilise les pwm hardware, plus précises que les pwm software. Les informations détaillées sont sur https://pypi.org/project/rpi-hardware-pwm/

Ajouter l’activation des pwm à config.txt :

dtoverlay=pwm-2chan,pin=12,func=4,pin2=13,func2=4

- sudo nano /boot/firmware/config.txt
ou sur les anciennes versions : sudo nano /boot/config.txt

Enregistrer et fermer (CTRL+X puis Y sur l’éditeur nano), redémarrer (sudo reboot) puis installer le module de gestion des pwm hardware, si ce n’est déjà fait :

- pip install rpi-hardware-pwm

Exemple de programme :

## 4 - Le Lidar

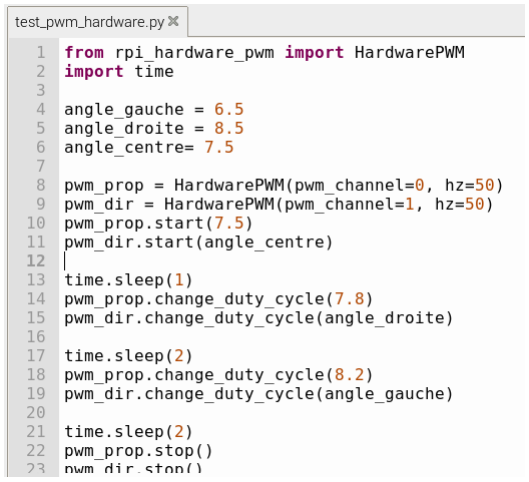
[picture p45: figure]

La bibliothèque semblant la plus intéressante, notamment pour la prise en compte du mode ExpressScan est la suivante : https://github.com/Roboticia/RPLidar/

Le module python s’installe de la manière suivante, si ce n’est déjà fait :

- $ pip install rplidar-roboticia -⁻break-system-packages

Le programme suivant permet de remettre le lidar à zéro, quel que soit la coupure du programme précédent.

Attention : il faut préciser le baudrate : la version A2M8 (noir et rouge) du RPLidar utilise une communication à 115200 baud et la version A2M12 (noir et violet) une communication à 256000 baud.

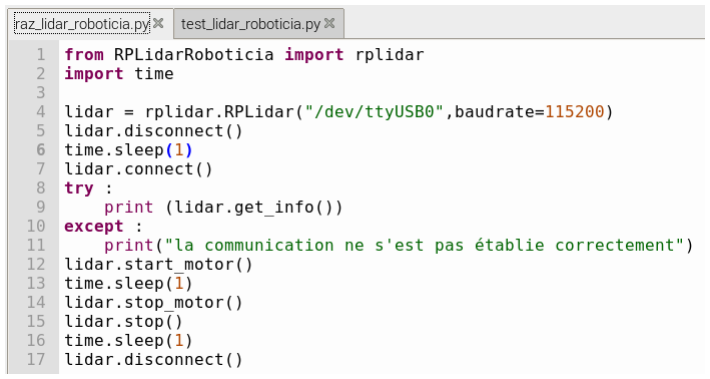
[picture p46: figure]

## 5 - Test des programmes de base CoVAPSy

Copier les programmes python du dépôt git sur la raspberry pi (en allant sur le git depuis le bureau de la voiture, soit en les chargeant sur un PC et en les copiant sur la raspberry via scp) :

https://github.com/ajuton-ens/CourseVoituresAutonomesSaclay/tree/main/Bibliotheques_logicielles/programmes_python_base_lidar_propulsion_direction_conduite (https://github.com/ajuton-ens/CourseVoituresAutonomesSaclay/tree/main/Bibliotheques_logicielles/programmes_python_base_lidar_propulsion_direction_conduite)

Programme test_direction.py

Lancer le programme test_direction.py et régler les butées (G/g pour déplacer la butée gauche et D/d pour déplacer la butée droite). Si le moteur guide la direction dans le sens inverse, ‘I’ permet d’inverser le sens.

Une fois la direction réglée, copier les nouveaux paramètres dans test_direction.py et dans

conduite_autonome_basique.py.

Programme test_propulsion.py

Faire de même pour la propulsion. Attention, pour régler la marche arrière, il faut d’abord demander un « freinage » (consigne -8000 à fond en arrière) puis repasser par 0 (consigne 0) puis demander une consigne raisonnable en marche arrière (-1000).

Une fois la direction réglée, copier les nouveaux paramètres dans test_direction.py et dans

conduite_autonome_basique.py.

Programme test_lidar.py

Régler la vitesse de transmission dans le programme (256000 pour les RPLIDAR A2-M12 115200 pour le RPLIDAR A2-M8). Lancer le programme.

Le programme raz_lidar.py (configuré avec la bonne vitesse de transmission) permet de remettre le lidar à 0 si il a été mal arrêté.

Une fois le lidar testé, copier la vitesse de transmission dans conduite_autonome_basique.py

Programme conduite_autonome_basique.py

Lancer le programme conduite_autonome_basique.py, la voiture doit se déplacer en asservissant sa position au milieu de la piste.

## Références :

[1]: CoVAPSy : Premiers programmes python sur la voiture réelle, T. Boulanger, E. Délègue,
K. Hoarau, A. Juton,
https://eduscol.education.fr/sti/si-ens-paris-saclay/ressources_pedagogiques/covapsy-premiersprogrammes-python-sur-voiture-reelle (https://eduscol.education.fr/sti/si-ens-paris-saclay/ressources_pedagogiques/covapsy-premiers-programmes-python-sur-voiture-reelle)

[2]: Dépôt github : https://github.com/ajuton-ens/CourseVoituresAutonomesSaclay/tree/main/Bibliotheques_logicielles/ (https://github.com/ajuton-ens/CourseVoituresAutonomesSaclay/tree/main/Bibliotheques_logicielles/programmes_python_base_lidar_propulsion_direction_conduite)

Ressource publiée sur Culture Sciences de l’Ingénieur : https://eduscol.education.fr/sti/si-ens-paris-saclay

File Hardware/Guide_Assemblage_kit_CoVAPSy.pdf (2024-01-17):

## Assemblage de l’électronique de la voiture type

## Identification des perçages des 2 plaques PMMA

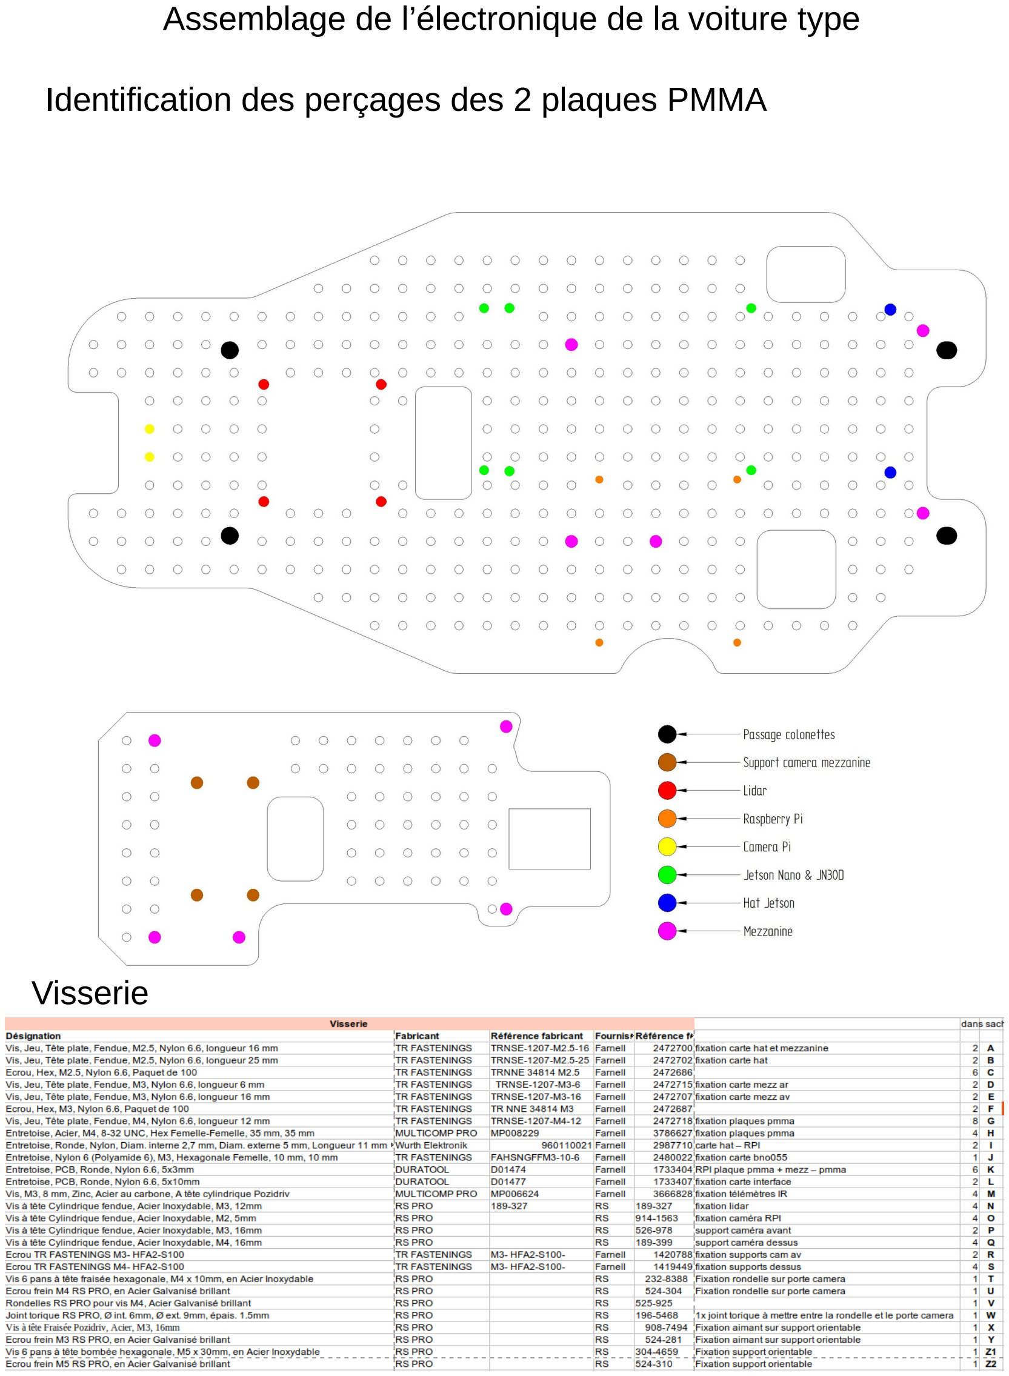
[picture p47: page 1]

## Visserie

Assemblage des entretoises sur la plaque PMMA principale

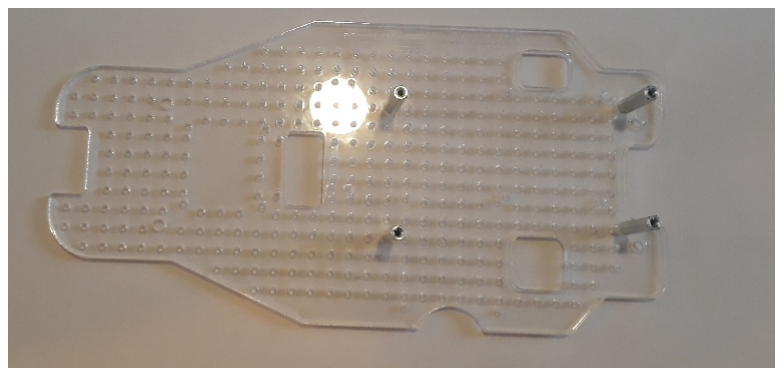
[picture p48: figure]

4 entretoises acier H
4 vis plastique M4 G

Fixation des 2 vis côté connecteur de la carte Raspberry Pi

2 vis plastique M2.5x16 mm | A
2 entretoises longueur 3 mm | K

# (ces entretroises peuvent avoir un diamètre intérieur 2,5 mm ou 3 mm)

2 écrous plastique M2,5 | C

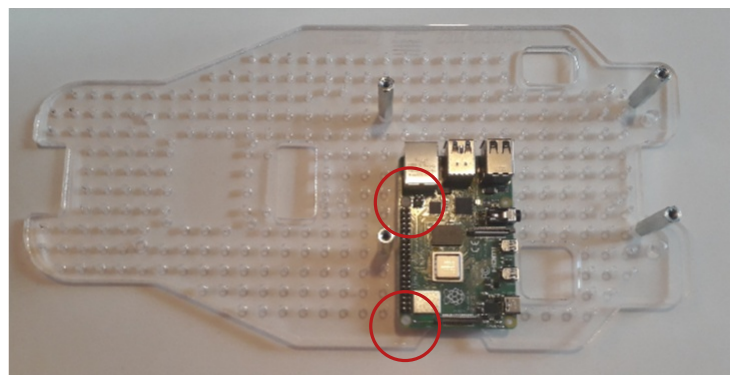
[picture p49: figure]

Fixation de la carte Hat sur la carte Raspberry Pi
Penser à connecter la nappe de la caméra si nécessaire avant d’installer la carte Hat

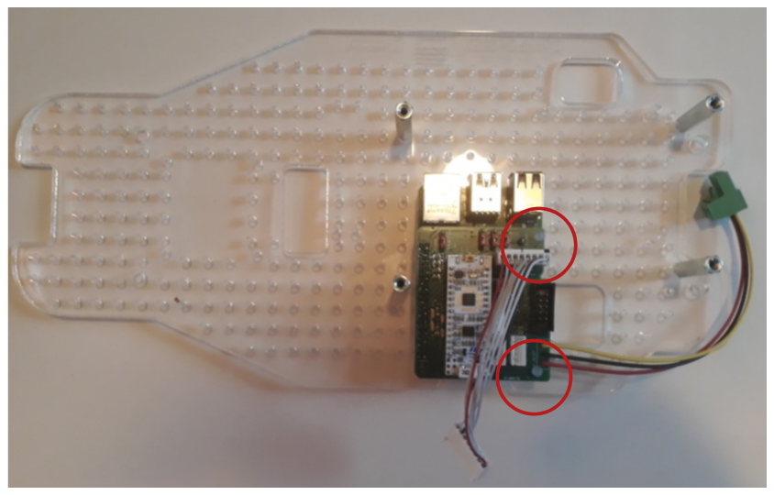
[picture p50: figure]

2 vis plastique M2.5x25 mm | B
2 entretoises longueur 11 mm | I
2 entretoises longueur 3 mm | K

# (ces entretroises peuvent avoir un diamètre intérieur 2,5 mm ou 3 mm)

2 écrous plastique M2,5 | C

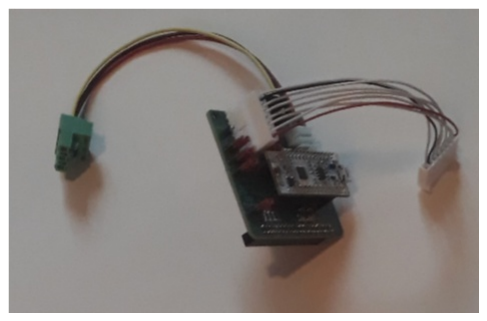
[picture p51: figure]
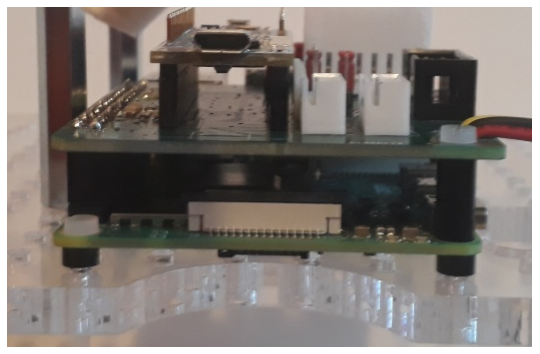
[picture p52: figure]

Clipsage de l’interrupteur sur la plaque PMMA mezzanine et fixation de la carte mezzanine

2 vis plastique M2.5 x 16 mm | A
2 écrous plastique M2,5 | C
2 vis plastique M3 x 16 mm | E
2 écrous plastique M3 | F
4 entretoises longueur 3 mm | K

Vis M2.5

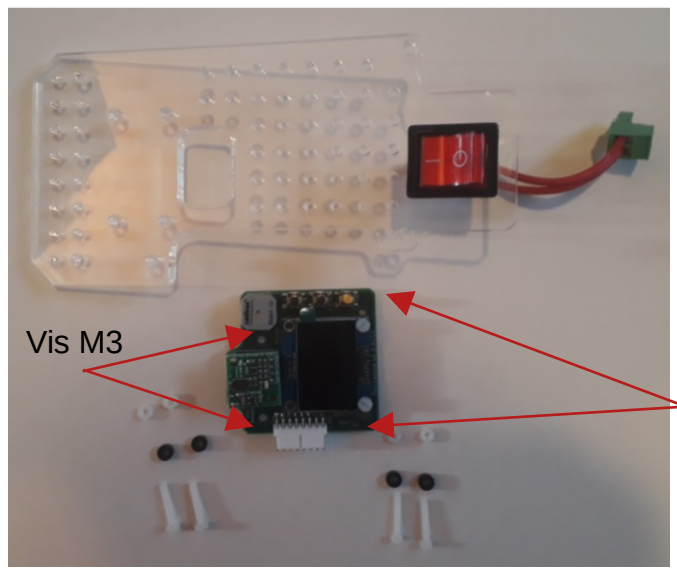
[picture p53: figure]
Vis M3

Assemblage des 2 plaques PMMA

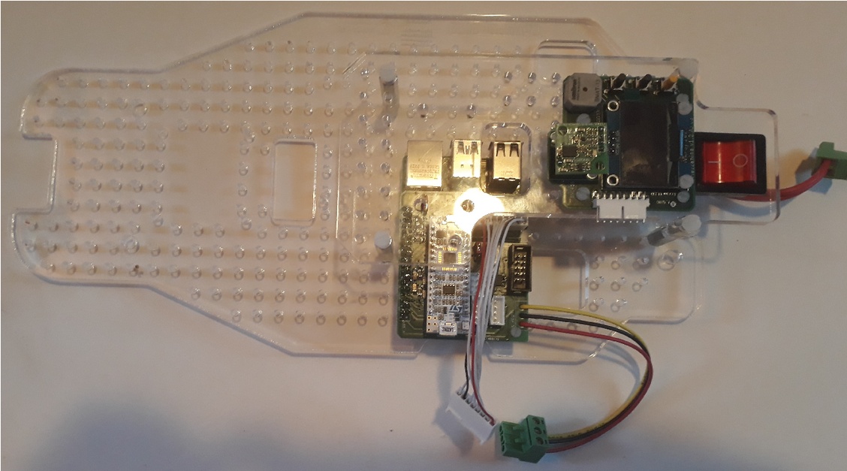
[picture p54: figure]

4 vis plastique M4 G

Ajout du lidar et du support caméra avant

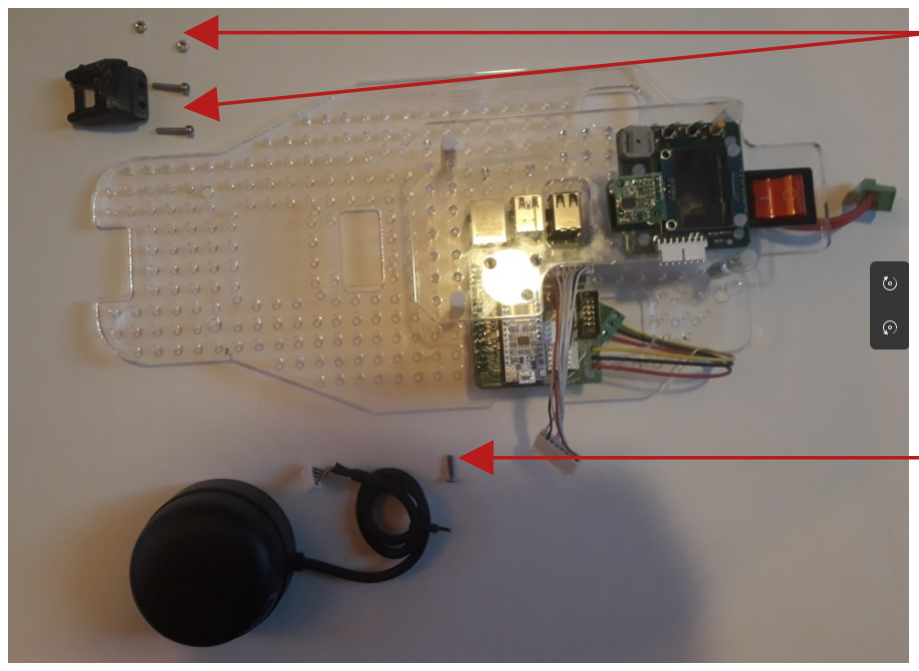
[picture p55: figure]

4 vis métal M3 x 12 mm | N
2 vis métal M3 x 16 mm | P
2 écrous métal M3 | R

Fixation de la caméra avant et fixation des câbles du lidar

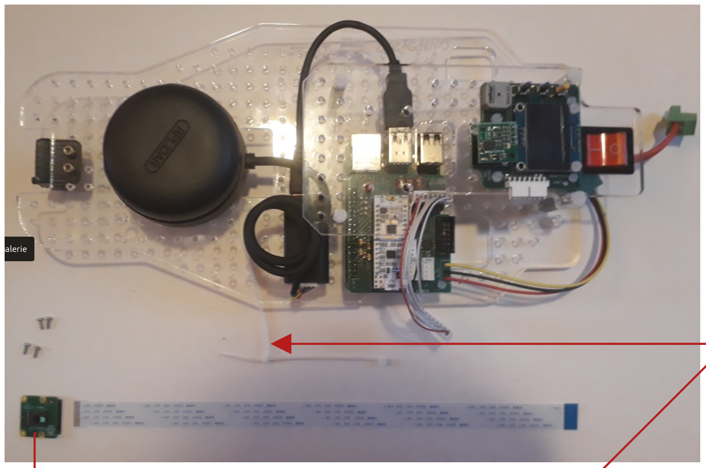
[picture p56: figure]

4 vis métal M2 | O

La caméra utilise la nappe de 30 cm pour aller jusqu’au connecteur caméra de la RPI.

2 colliers plastiques issus du kit TT-02

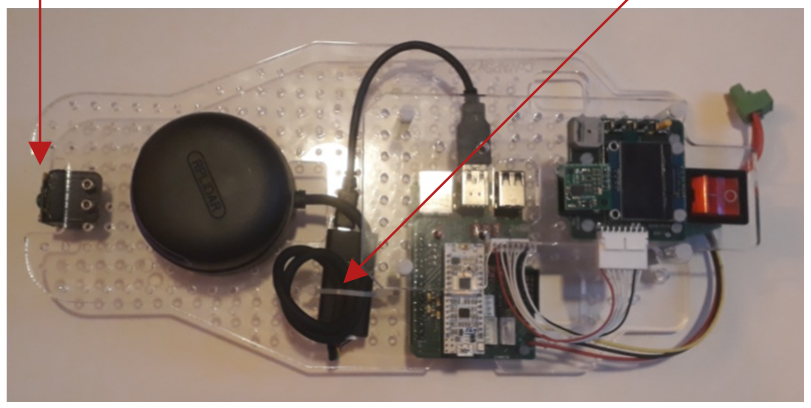
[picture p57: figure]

Il est plus facile de fixer la carte interface si les suspensions utilisent les trous supérieurs

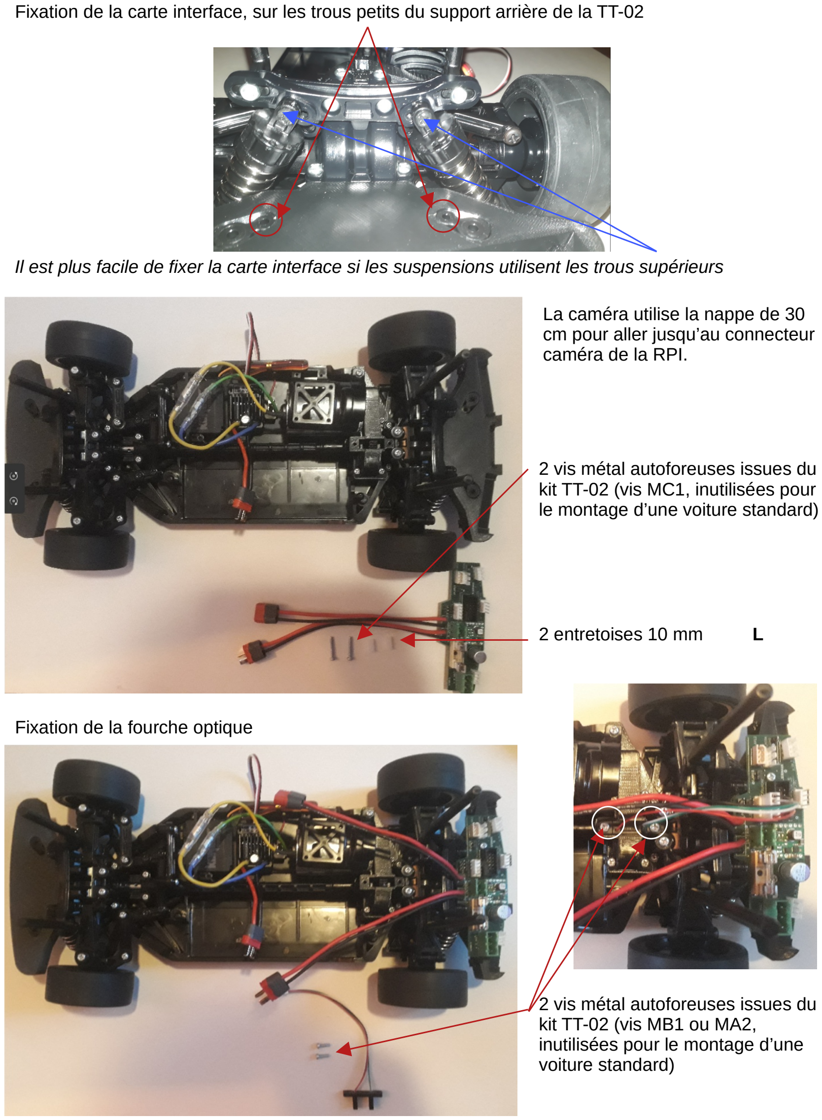
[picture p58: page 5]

La caméra utilise la nappe de 30 cm pour aller jusqu’au connecteur caméra de la RPI.

Fixation de la carte interface, sur les trous petits du support arrière de la TT-02

2 vis métal autoforeuses issues du kit TT-02 (vis MC1, inutilisées pour le montage d’une voiture standard)

2 entretoises 10 mm | L

Fixation de la fourche optique

2 vis métal autoforeuses issues du kit TT-02 (vis MB1 ou MA2, inutilisées pour le montage d’une voiture standard)

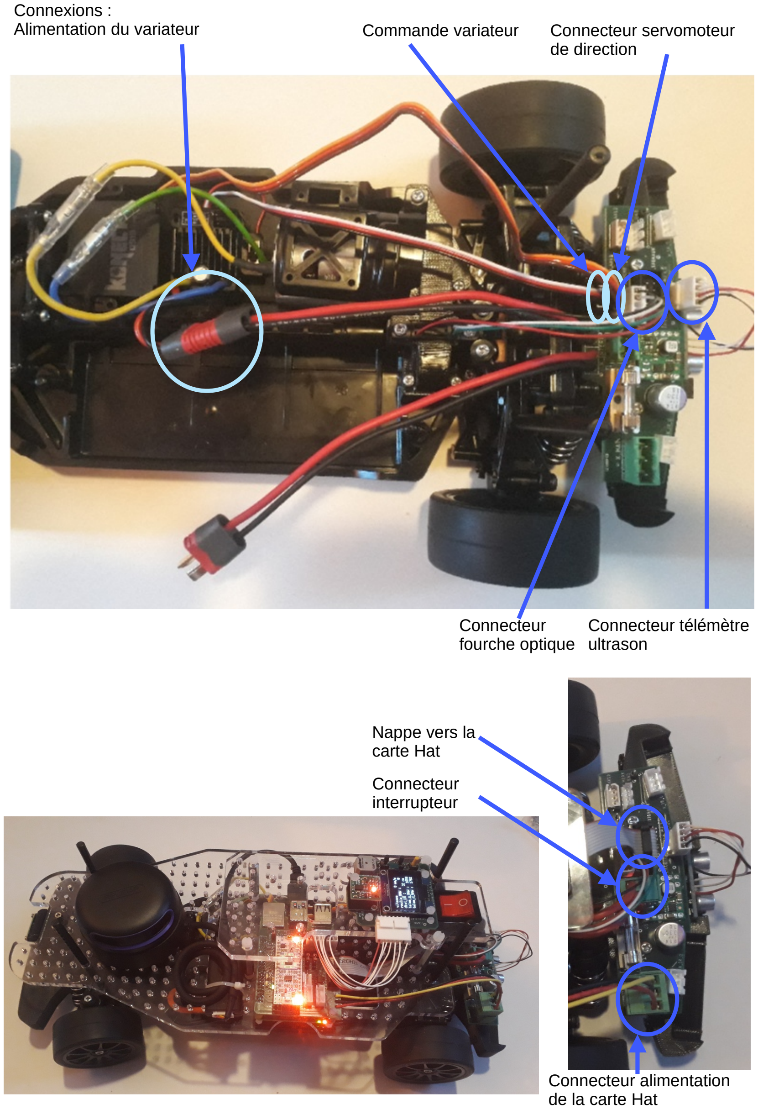
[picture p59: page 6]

Connexions :
Alimentation du variateur | Commande variateur | Connecteur servomoteur
| | de direction

Connecteur télémètre
ultrason

Connecteur
fourche optique

Nappe vers la
carte Hat

Connecteur alimentation
de la carte Hat

Connecteur
interrupteur

Montage du support caméra supérieure

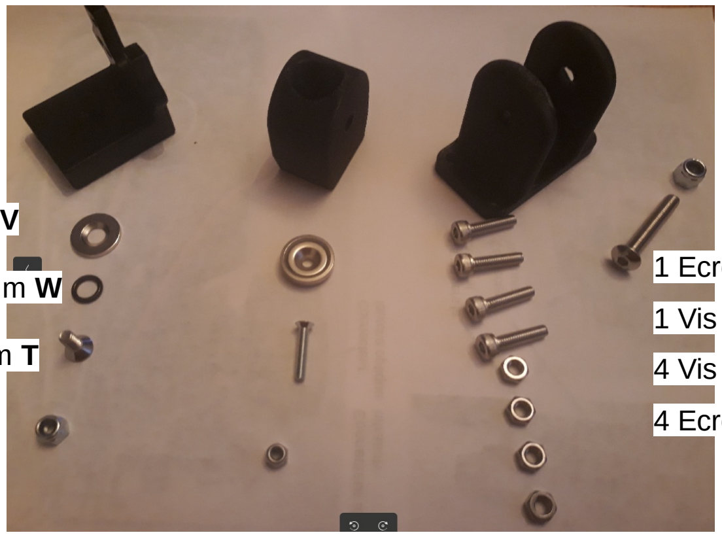
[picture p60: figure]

4 Vis acier M4 x 16mm Q

support caméra
supérieure

4 Ecrous M4

1 Vis 6 pans M4 x 10mm | T
1 Ecrou frein M4 | S
1 Rondelle pour vis M4 | V
1 Joint torique Ø int. 6Mm | W

1 Vis à tête Fraisée Acier, M3, 16mm X 1 Ecrou frein M3 Y

1 Vis 6 pans M5 x 30mm | Z1
1 Ecrou frein M5 | Z2

Support orientable
et aimant

Porte-caméra

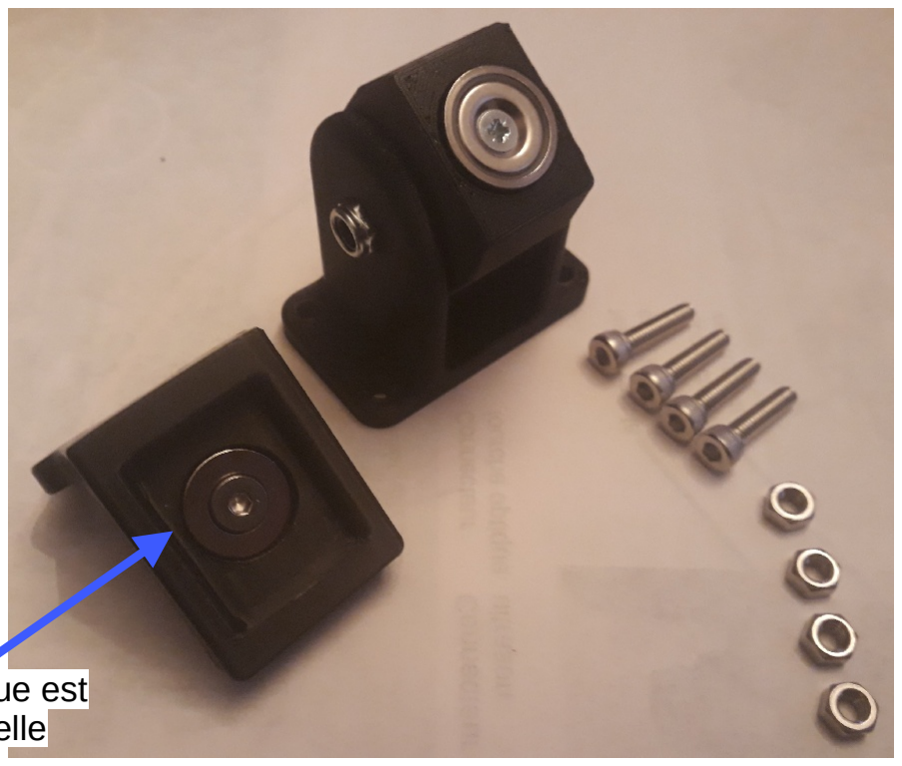
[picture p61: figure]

Le joint torique est
sous la rondelle

Les 4 Vis/écrous servent
à fixer le support caméra
sur la plaque PMMA
mezzanine.

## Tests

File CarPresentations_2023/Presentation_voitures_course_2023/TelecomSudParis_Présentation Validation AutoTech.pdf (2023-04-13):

# AutoTech

## Equipe de Télécom SudParis

# Hardware

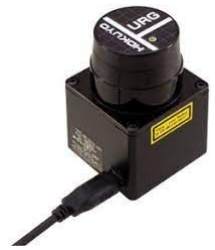
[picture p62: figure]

- Jetson nano

■ Lidar Hokuyo

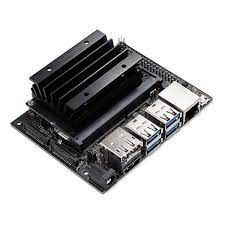
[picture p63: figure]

- Arduino nano

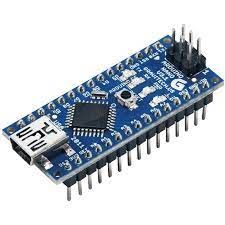
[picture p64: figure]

■ 2 Batteries lipo 12V

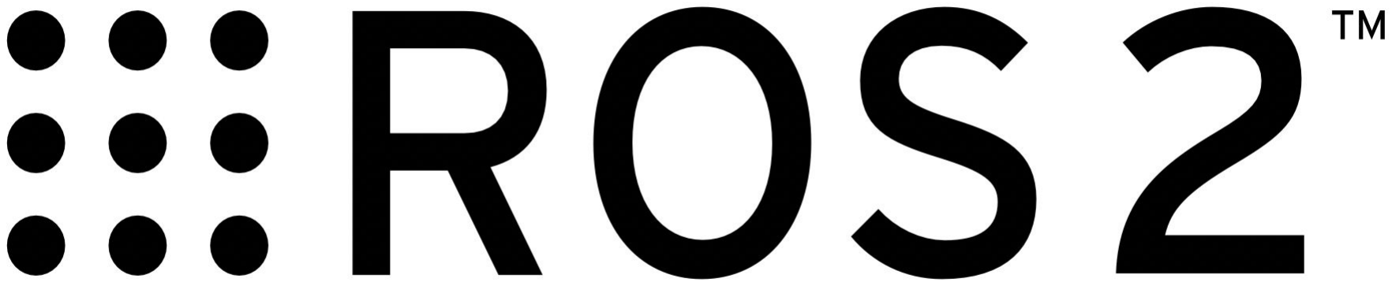
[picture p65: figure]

- Système d’exploitation pour la Robotique
- Architecture en noeuds : lien entre les différents composants

## L’Architecture

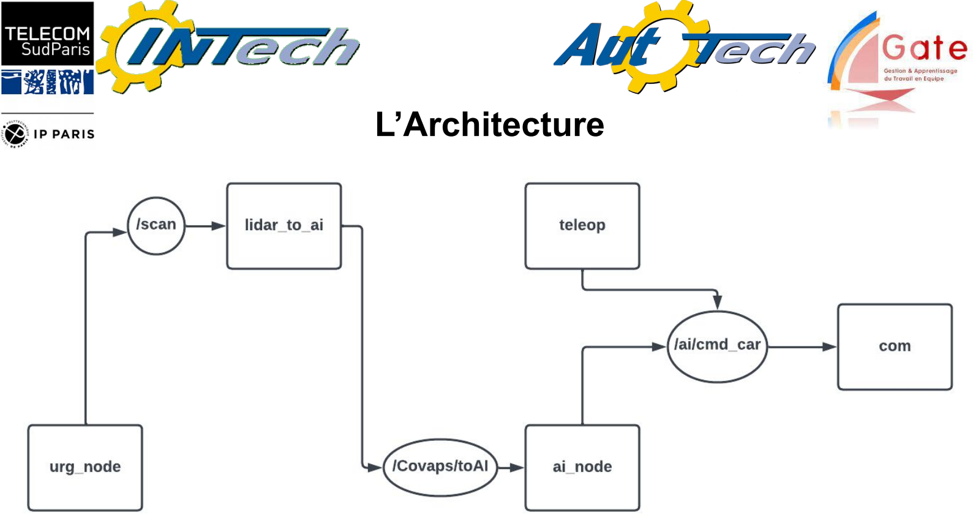
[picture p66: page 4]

# L’Intelligence Artificielle

## L’Environnement

- Basé sur highway-env
- Rajouts : circuits générés aléatoirement, lidar, collision, adversaires intelligents, obstacles.

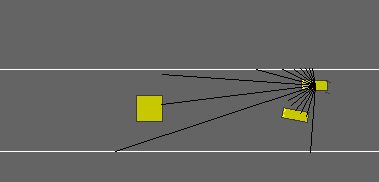
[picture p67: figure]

## L’Entraînement

Reinforcement Learning avec :

- Algorithme (PPO) de stable-baselines3
- Gym (API)
- Optuna (Optimisation des hyperparamètres et rewards)

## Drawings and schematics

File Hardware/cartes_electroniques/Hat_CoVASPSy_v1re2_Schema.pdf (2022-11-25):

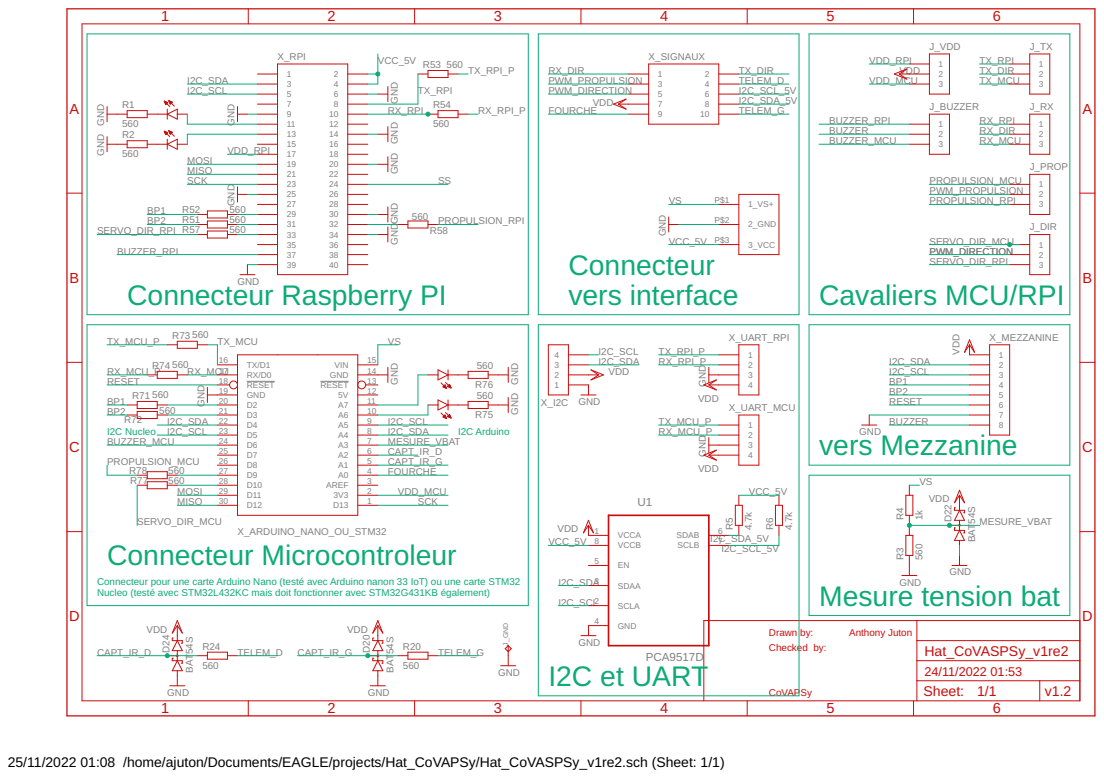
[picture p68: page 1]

Connecteur pour une carte Arduino Nano (testé avec Arduino nanon 33 IoT) ou une carte STM32
Nucleo (testé avec STM32L432KC mais doit fonctionner avec STM32G431KB également)

Drawn by: Checked by: CoVAPSy

25/11/2022 01:08 /home/ajuton/Documents/EAGLE/projects/Hat_CoVAPSy/Hat_CoVASPSy_v1re2.sch (Sheet: 1/1)

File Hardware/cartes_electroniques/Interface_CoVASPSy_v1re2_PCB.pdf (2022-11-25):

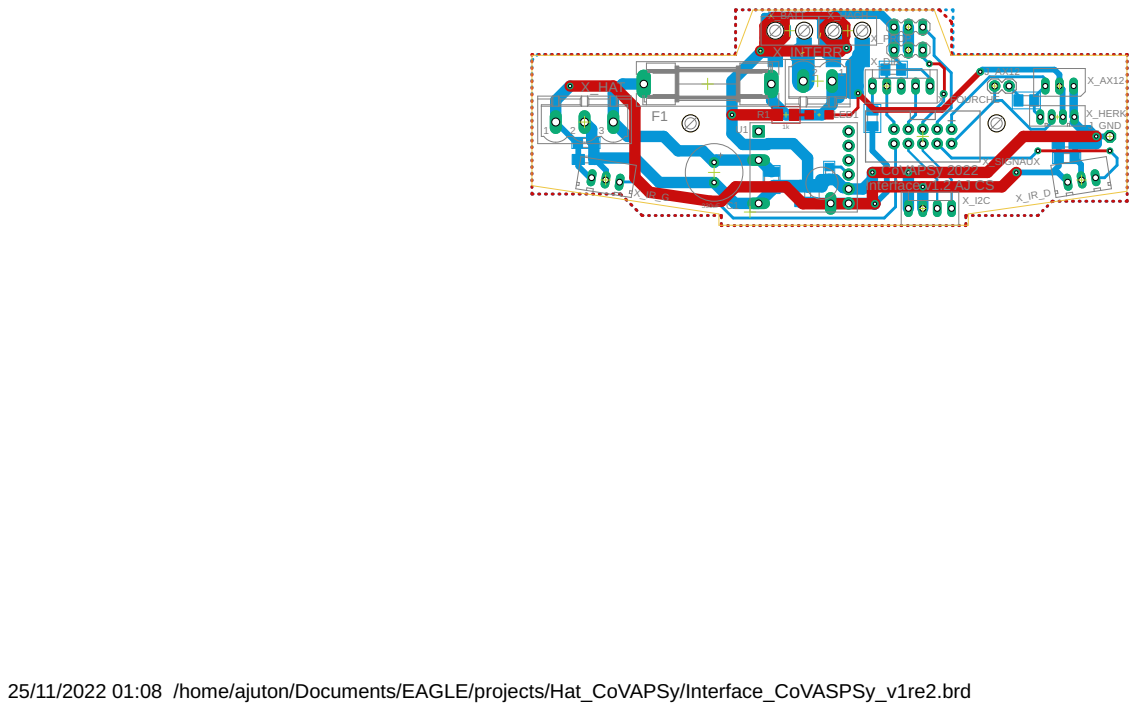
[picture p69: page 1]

R1 | LED1

25/11/2022 01:08 /home/ajuton/Documents/EAGLE/projects/Hat_CoVAPSy/Interface_CoVASPSy_v1re2.brd

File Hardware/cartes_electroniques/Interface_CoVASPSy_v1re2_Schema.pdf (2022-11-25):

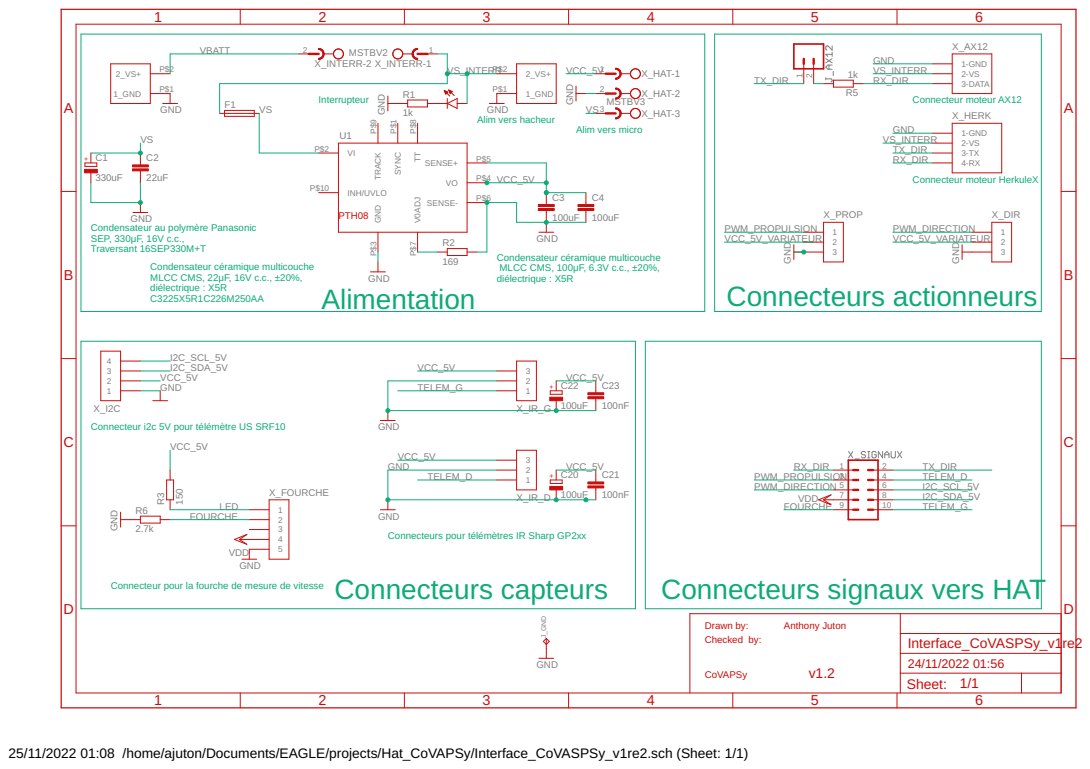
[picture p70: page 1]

Condensateur au polymère Panasonic SEP, 330μF, 16V c.c., Traversant 16SEP330M+T

Condensateur céramique multicouche MLCC CMS, 100μF, 6.3V c.c., ±20%, diélectrique : X5R

Condensateur céramique multicouche MLCC CMS, 22μF, 16V c.c., ±20%, diélectrique : X5R

Connecteur i2c 5V pour télémètre US SRF10

Connecteur pour la fourche de mesure de vitesse

Drawn by: Checked by: CoVAPSy Anthony Juton v1.2

Sheet: 1/1

25/11/2022 01:08 /home/ajuton/Documents/EAGLE/projects/Hat_CoVAPSy/Interface_CoVASPSy_v1re2.sch (Sheet: 1/1)

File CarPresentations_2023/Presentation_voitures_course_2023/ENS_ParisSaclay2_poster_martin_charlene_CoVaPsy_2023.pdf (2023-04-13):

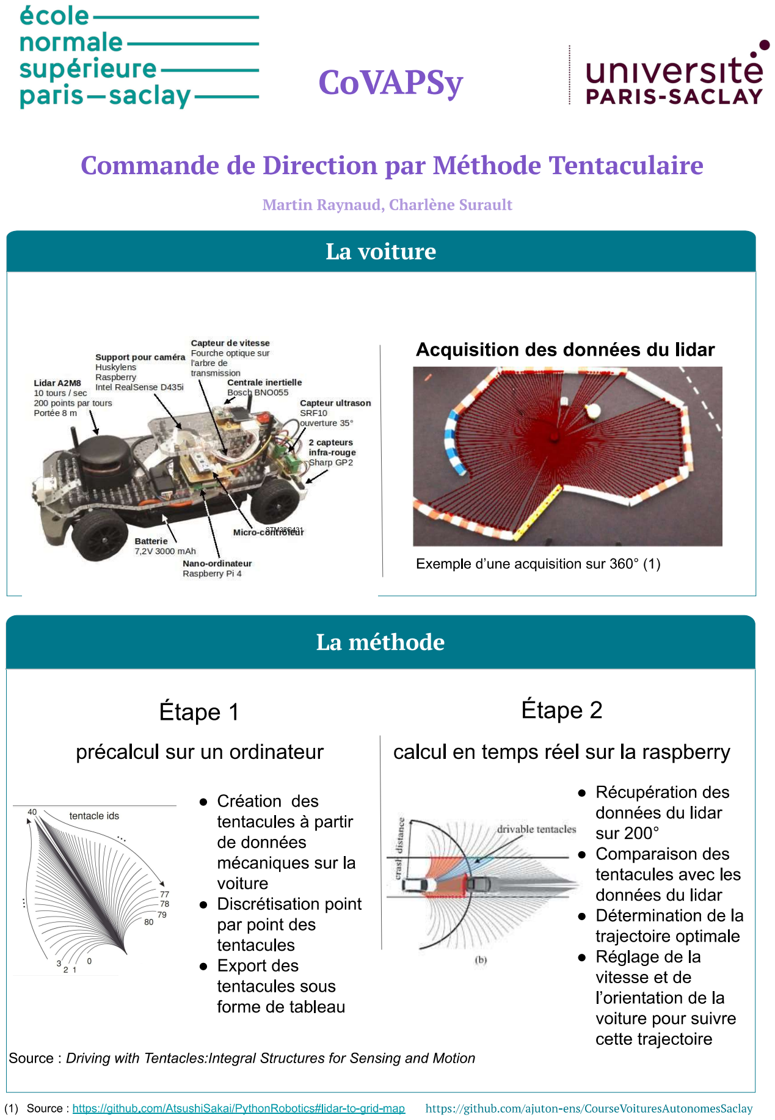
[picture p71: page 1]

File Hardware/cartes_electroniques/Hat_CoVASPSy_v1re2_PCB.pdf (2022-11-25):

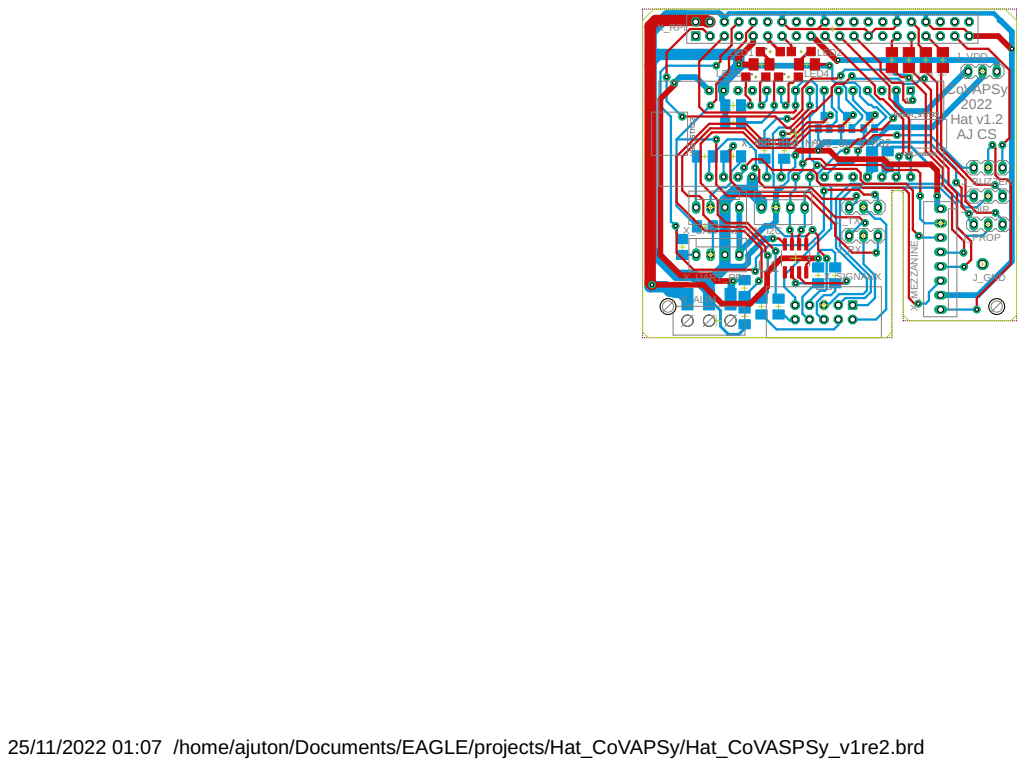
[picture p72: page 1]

25/11/2022 01:07 /home/ajuton/Documents/EAGLE/projects/Hat_CoVAPSy/Hat_CoVASPSy_v1re2.brd

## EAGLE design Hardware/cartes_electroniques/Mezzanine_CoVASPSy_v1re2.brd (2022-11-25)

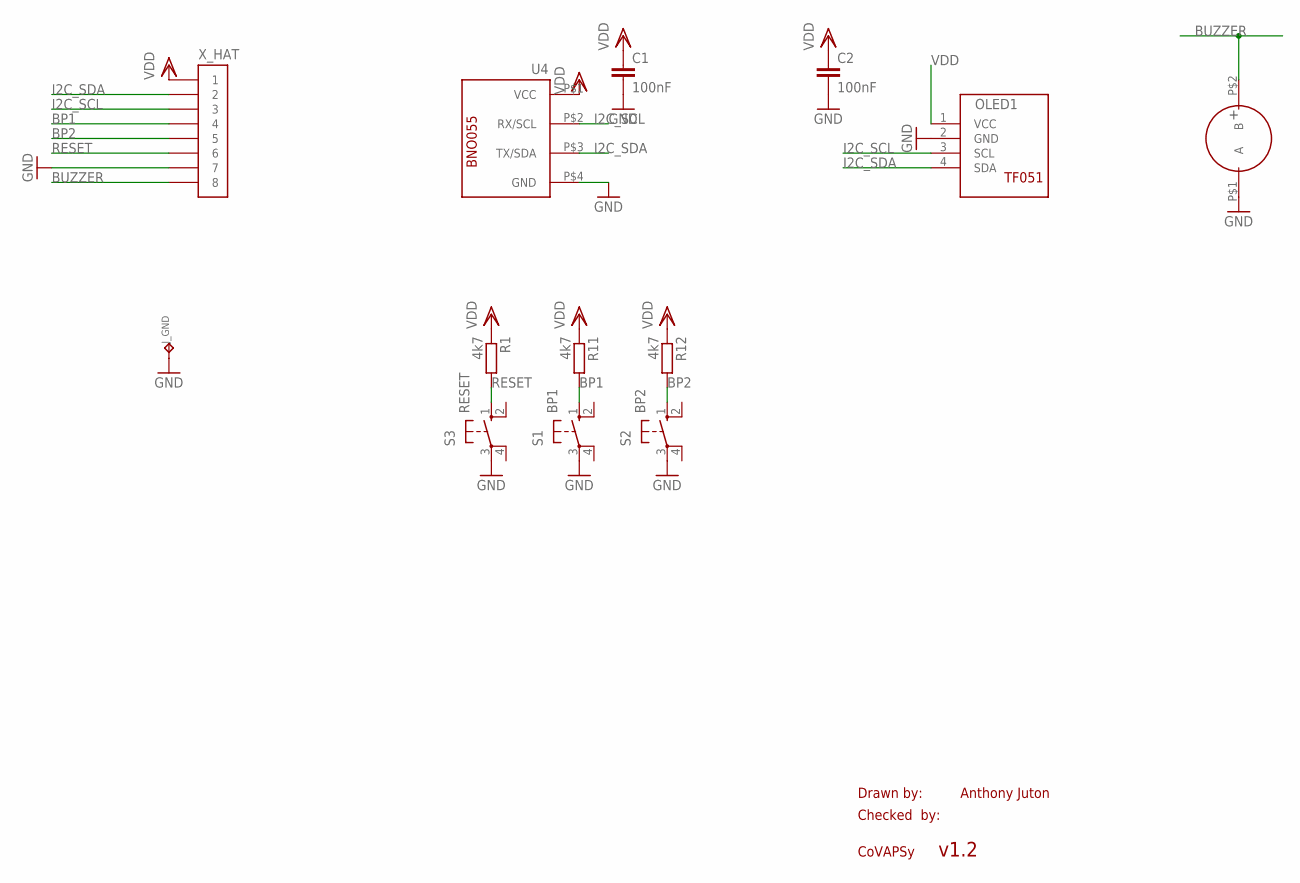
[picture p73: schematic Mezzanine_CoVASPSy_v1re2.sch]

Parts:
BUZZER: BUZZER_SMA13_P75; BUZZER_SMA_13_P75
C1, C2: 100nF; C1206K
J_GND: COSSE_POIGN; COSSE_POIGNARD
OLED1: ECRAN_OLED_TF051
R1, R11, R12: 4k7; M1206
S1: BP1; B3F-10XX
S2: BP2; B3F-10XX
S3: RESET; B3F-10XX
U4: MODULE_BNO055
X_HAT: MOLEX_8_COUDE

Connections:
BP1: R11.2, S1.1 (S), X_HAT.P$4 (4)
BP2: R12.2, S2.1 (S), X_HAT.P$5 (5)
BUZZER: BUZZER.P$2 (B), X_HAT.P$8 (8)
GND: BUZZER.P$1 (A), C1.2, C2.2, J_GND.P$1, OLED1.2 (GND), S1.3, S2.3, S3.3, U4.P$4 (GND), X_HAT.P$7 (7)
I2C_SCL: OLED1.3 (SCL), U4.P$2 (RX/SCL), X_HAT.P$3 (3)
I2C_SDA: OLED1.4 (SDA), U4.P$3 (TX/SDA), X_HAT.P$2 (2)
RESET: R1.2, S3.1 (S), X_HAT.P$6 (6)
VDD: C1.1, C2.1, OLED1.1 (VCC), R1.1, R11.1, R12.1, U4.P$1 (VCC), X_HAT.P$1 (1)

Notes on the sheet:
Drawn by:
Checked by:
CoVAPSy
Anthony Juton
v1.2

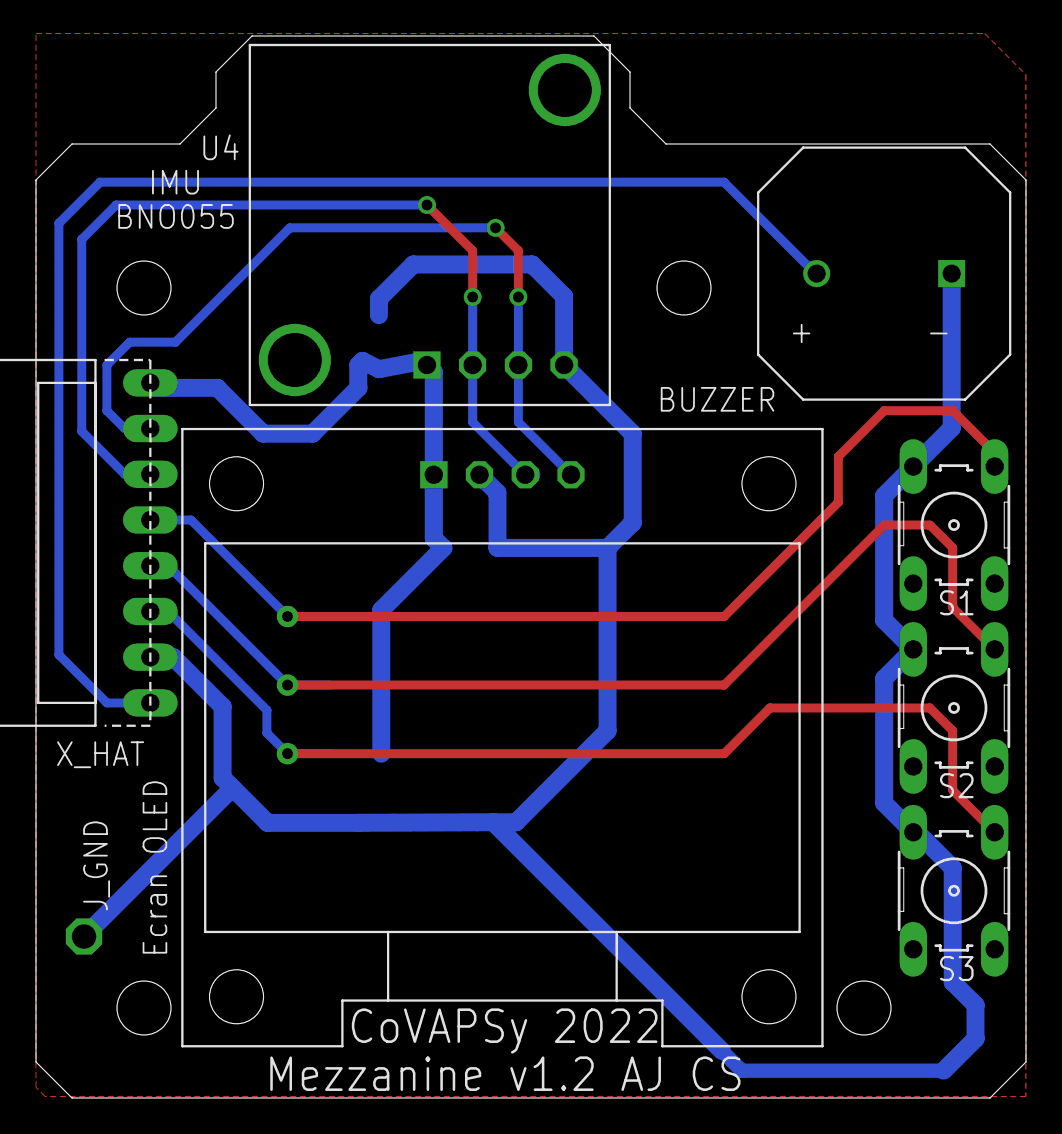
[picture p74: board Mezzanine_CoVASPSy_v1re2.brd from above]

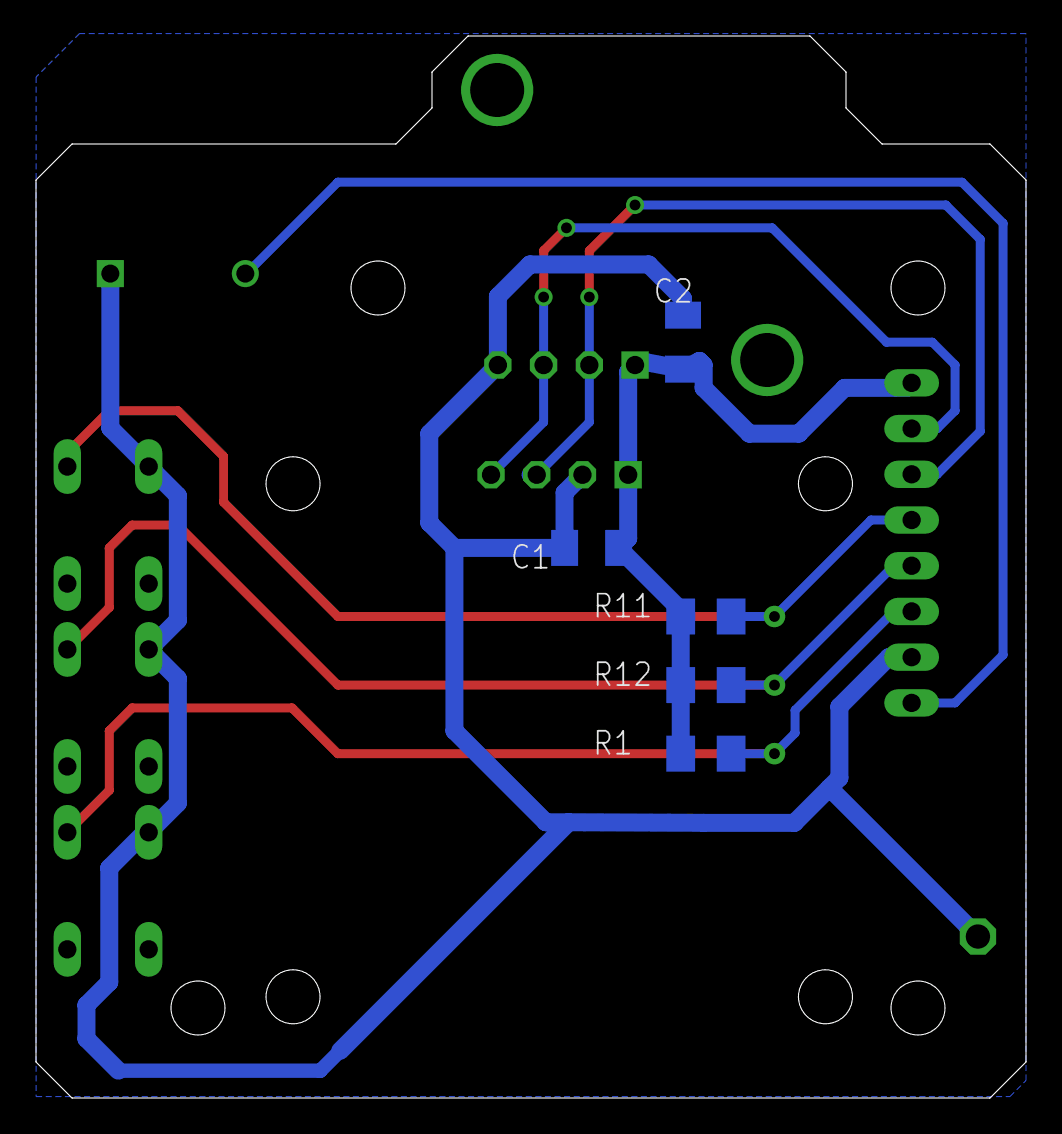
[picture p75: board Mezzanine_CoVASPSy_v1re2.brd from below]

Board: 2 copper layers, 55.0 x 59.0 mm, 13 parts (5 on the bottom side), 8 nets.

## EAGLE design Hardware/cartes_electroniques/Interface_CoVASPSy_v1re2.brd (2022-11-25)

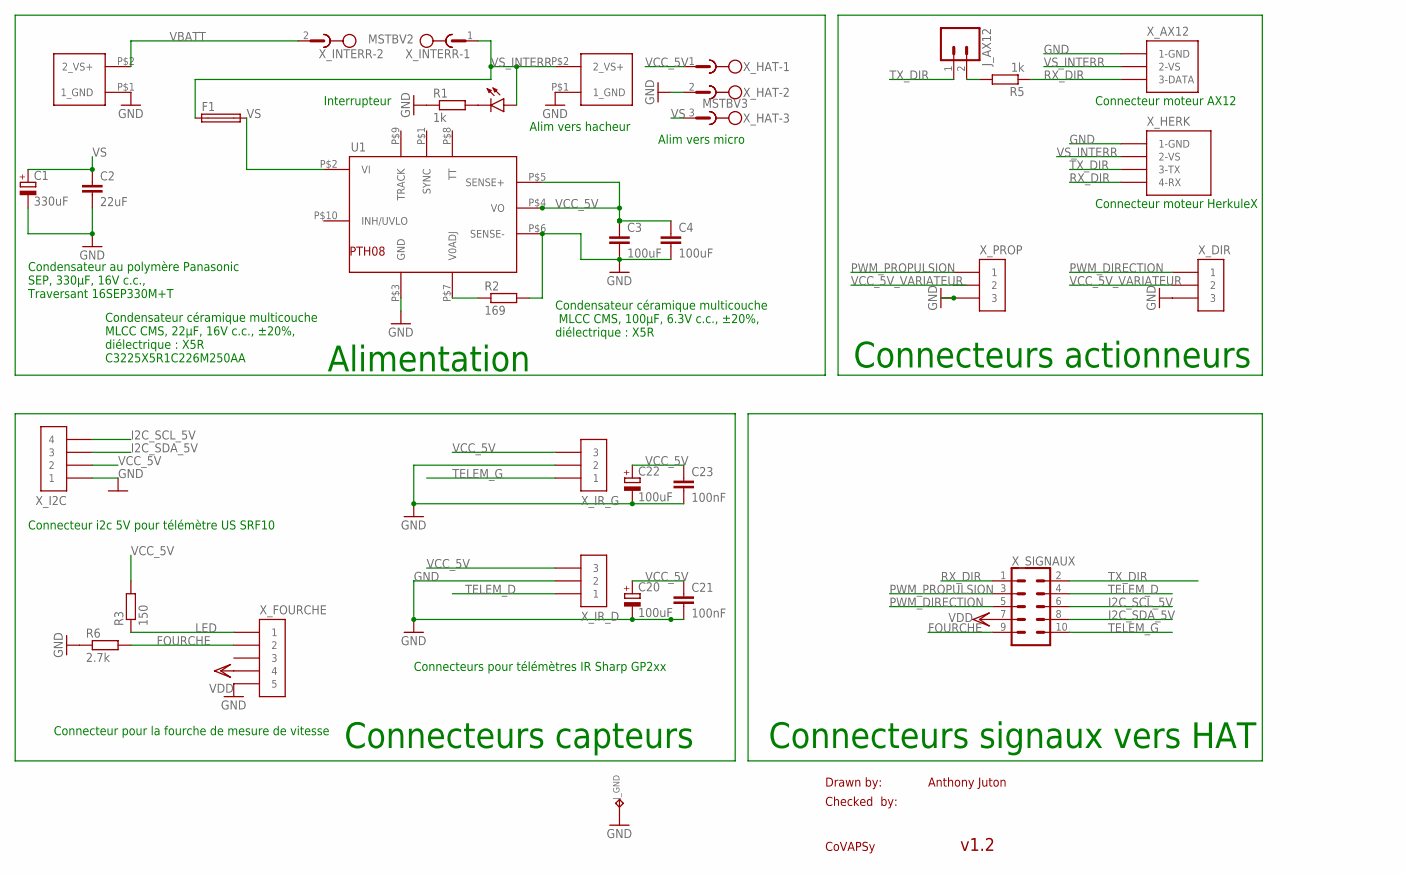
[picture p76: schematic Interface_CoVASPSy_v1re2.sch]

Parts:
C1: 330uF; E3,5-10
C2: 22uF; C1210
C3, C4: 100uF; C1206K
C20, C22: 100uF; A/3216-18W
C21, C23: 100nF; C1206
F1: SH22,5
J_AX12: CONN_02; 1X02
J_GND: COSSE_POIGN; COSSE_POIGNARD
LED1: LEDSML1206; SML1206
R1, R5: 1k; M1206
R2: 169; R0805
R3: 150; M1206
R6: 2.7k; M1206
U1: CONV_TI_PTH08; CONV_TI_PTH8
X_AX12: MOLEX_AX12
X_BATT: CONN_ALIM_TROU
X_DIR: CAVALIER_3
X_FOURCHE: MOLEX_5_DROIT
X_HACH: CONN_ALIM_TROU
X_HAT: MSTBV3
X_HERK: TE_HERKULEX
X_I2C: MOLEX_4_DROIT
X_INTERR: MSTBV2
X_IR_D: JST_3
X_IR_G: JST_3
X_PROP: CAVALIER_3
X_SIGNAUX: CONN_05X2SHD; 2X5-SHROUDED

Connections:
FOURCHE: R6.2, X_FOURCHE.P$2 (2), X_SIGNAUX.9
GND: C1.-, C2.2, C3.2, C4.2, C20.-, C21.2, C22.-, C23.2, J_GND.P$1, R1.1, R2.2, R6.1, U1.P$3 (GND), U1.P$6 (SENSE-), X_AX12.P$1 (1-GND), X_BATT.P$1 (1_GND), X_DIR.P$3 (3), X_FOURCHE.P$5 (5), X_HACH.P$1 (1_GND), X_HAT.2, X_HERK.P$1 (1-GND), X_I2C.P$1 (1), X_IR_D.P$2 (2), X_IR_G.P$2 (2), X_PROP.P$3 (3)
I2C_SCL_5V: X_I2C.P$4 (4), X_SIGNAUX.6
I2C_SDA_5V: X_I2C.P$3 (3), X_SIGNAUX.8
LED: R3.1, X_FOURCHE.P$1 (1)
unnamed: LED1.C, R1.2
unnamed: J_AX12.2, R5.2
unnamed: R2.1, U1.P$7 (V0ADJ)
PWM_DIRECTION: X_DIR.P$1 (1), X_SIGNAUX.5
PWM_PROPULSION: X_PROP.P$1 (1), X_SIGNAUX.3
RX_DIR: R5.1, X_AX12.P$3 (3-DATA), X_HERK.P$4 (4-RX), X_SIGNAUX.1
TELEM_D: X_IR_D.P$1 (1), X_SIGNAUX.4
TELEM_G: X_IR_G.P$1 (1), X_SIGNAUX.10
TX_DIR: J_AX12.1, X_HERK.P$3 (3-TX), X_SIGNAUX.2
VBATT: X_BATT.P$2 (2_VS+), X_INTERR.2
VCC_5V: C3.1, C4.1, C20.+, C21.1, C22.+, C23.1, R3.2, U1.P$4 (VO), U1.P$5 (SENSE+), X_HAT.1, X_I2C.P$2 (2), X_IR_D.P$3 (3), X_IR_G.P$3 (3)
VCC_5V_VARIATEUR: X_DIR.P$2 (2), X_PROP.P$2 (2)
VDD: X_FOURCHE.P$4 (4), X_SIGNAUX.7
VS: C1.+, C2.1, F1.2, U1.P$2 (VI), X_HAT.3
VS_INTERR: F1.1, LED1.A, X_AX12.P$2 (2-VS), X_HACH.P$2 (2_VS+), X_HERK.P$2 (2-VS), X_INTERR.1

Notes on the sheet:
Drawn by:
Checked by:
CoVAPSy
Anthony Juton
v1.2
Connecteur moteur AX12
Connecteur pour la fourche de mesure de vitesse
Connecteur moteur HerkuleX
Connecteurs actionneurs
Condensateur au polymère Panasonic SEP, 330μF, 16V c.c., Traversant 16SEP330M+T
Condensateur céramique multicouche MLCC CMS, 22μF, 16V c.c., ±20%, diélectrique : X5R C3225X5R1C226M250AA
Condensateur céramique multicouche MLCC CMS, 100μF, 6.3V c.c., ±20%, diélectrique : X5R
Alimentation
Alim vers hacheur
Interrupteur
Alim vers micro
Connecteurs capteurs
Connecteur i2c 5V pour télémètre US SRF10
Connecteurs pour télémètres IR Sharp GP2xx
Connecteurs signaux vers HAT

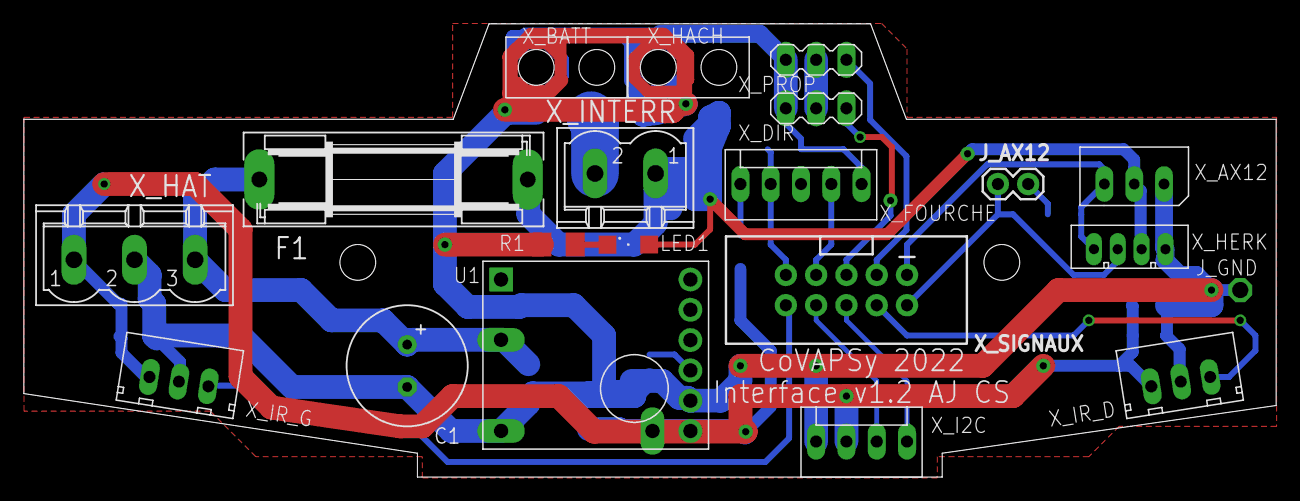
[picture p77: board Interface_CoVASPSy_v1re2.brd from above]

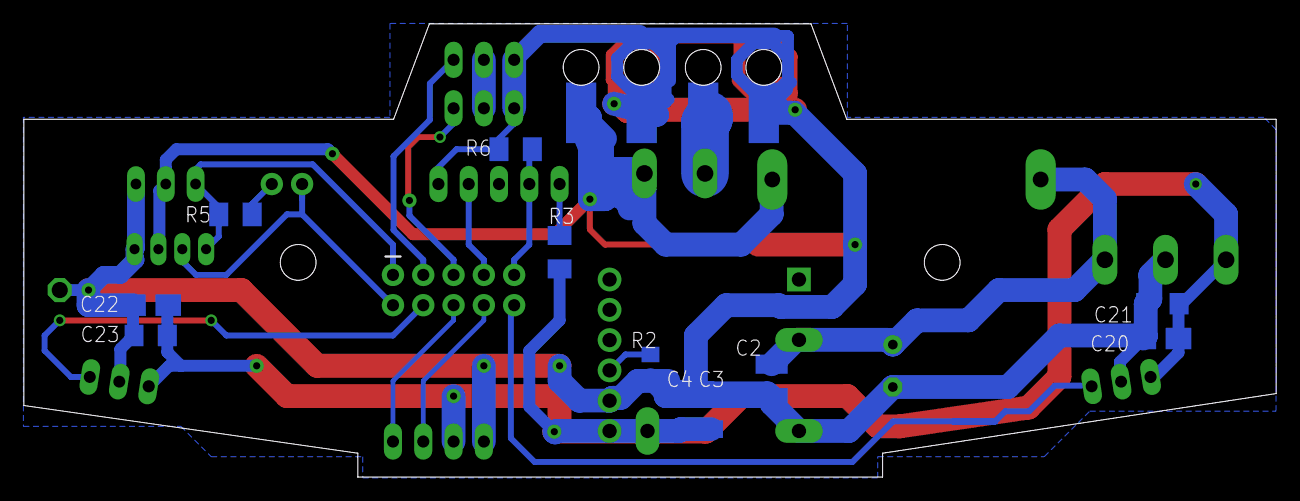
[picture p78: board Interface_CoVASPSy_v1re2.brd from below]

Board: 2 copper layers, 105.0 x 38.0 mm, 31 parts (11 on the bottom side), 20 nets.

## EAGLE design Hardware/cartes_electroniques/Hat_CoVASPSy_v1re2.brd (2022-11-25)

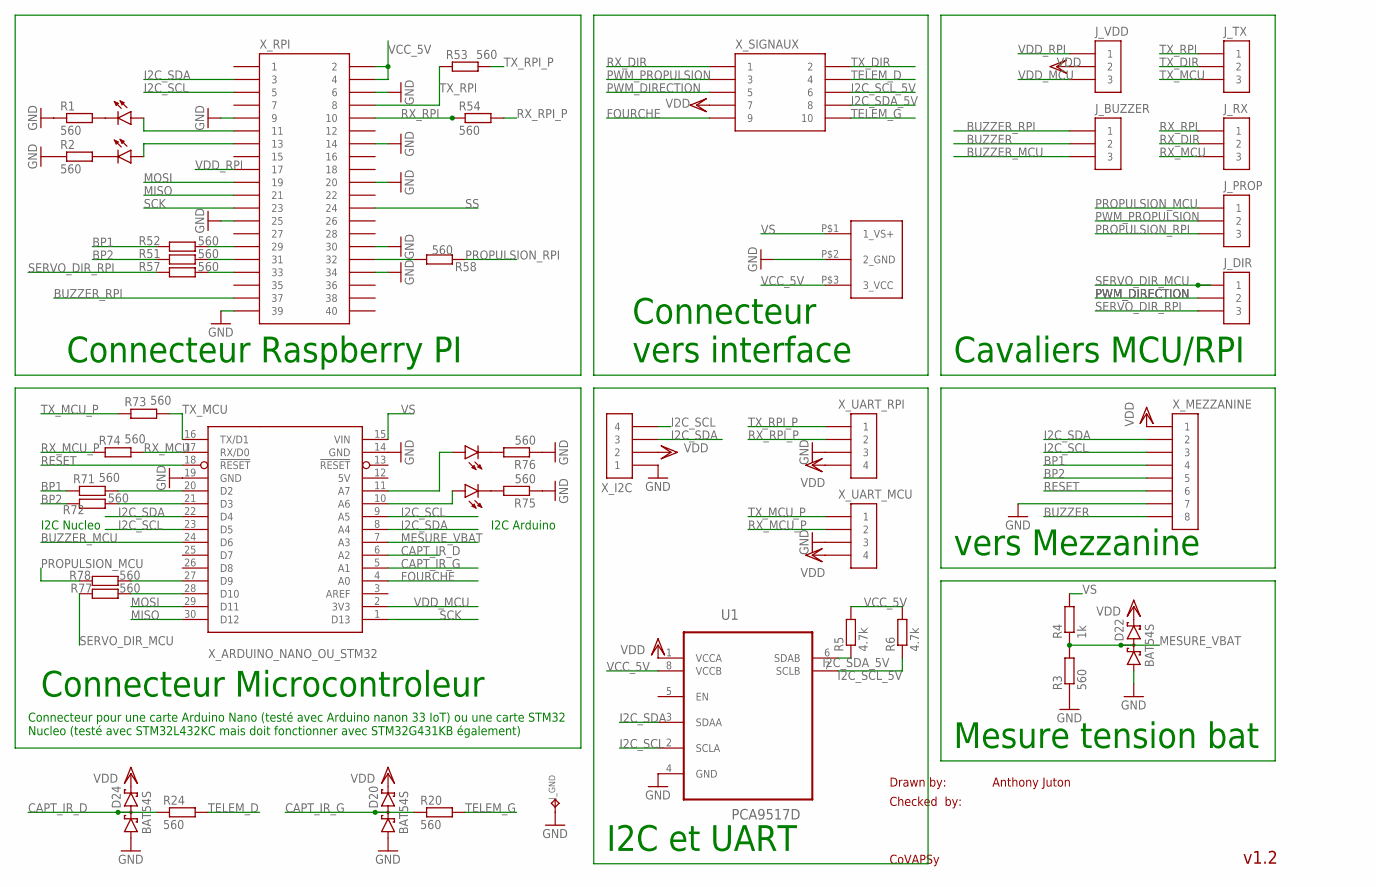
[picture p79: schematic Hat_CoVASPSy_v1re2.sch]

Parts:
D20, D22, D24: BAT54S; SOT23
J_BUZZER: CAVALIER_3
J_DIR: CAVALIER_3
J_GND: COSSE_POIGN; COSSE_POIGNARD
J_PROP: CAVALIER_3
J_RX: CAVALIER_3
J_TX: CAVALIER_3
J_VDD: CAVALIER_3
LED1, LED2, LED3, LED4: LEDSML1206; SML1206
R1, R2, R3, R20, R24, R51, R52, R53, R54, R57, R58, R71, R72, R73, R74, R75, R76, R77, R78: 560; M1206
R4: 1k; M1206
R5, R6: 4.7k; M1206
U1: PCA9517D; SOIC127P600X175-8N
X_ALIM: CONN_ALIM_3TROUS
X_ARDUINO_NANO_OU_STM32: ARDUINO_NANO_STM32_NUCLEO
X_I2C: MOLEX_4_DROIT
X_MEZZANINE: MOLEX_8_DROIT
X_RPI: HEADER_20X2
X_SIGNAUX: HEADER_5X2
X_UART_MCU: MOLEX_4_DROIT
X_UART_RPI: MOLEX_4_DROIT

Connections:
5V: X_ARDUINO_NANO_OU_STM32.12 (5V)
BP1: R52.1, R71.1, X_MEZZANINE.P$4 (4)
BP2: R51.1, R72.1, X_MEZZANINE.P$5 (5)
BUZZER: J_BUZZER.P$2 (2), X_MEZZANINE.P$8 (8)
BUZZER_MCU: J_BUZZER.P$3 (3), X_ARDUINO_NANO_OU_STM32.24 (D6)
BUZZER_RPI: J_BUZZER.P$1 (1), X_RPI.P$37 (37)
CAPT_IR_D: D24.3 (C1A2), R24.1, X_ARDUINO_NANO_OU_STM32.6 (A2)
CAPT_IR_G: D20.3 (C1A2), R20.1, X_ARDUINO_NANO_OU_STM32.5 (A1)
FOURCHE: X_ARDUINO_NANO_OU_STM32.4 (A0), X_SIGNAUX.P$9 (9)
GND: D20.1 (A1), D22.1 (A1), D24.1 (A1), J_GND.P$1, R1.1, R2.1, R3.1, R75.1, R76.1, U1.4 (GND), X_ALIM.P$2 (2_GND), X_ARDUINO_NANO_OU_STM32.14 (GND), X_ARDUINO_NANO_OU_STM32.19 (GND), X_I2C.P$1 (1), X_MEZZANINE.P$7 (7), X_RPI.P$6 (6), X_RPI.P$9 (9), X_RPI.P$14 (14), X_RPI.P$20 (20), X_RPI.P$25 (25), X_RPI.P$30 (30), X_RPI.P$34 (34), X_RPI.P$39 (39), X_UART_MCU.P$3 (3), X_UART_RPI.P$3 (3)
I2C_SCL: U1.2 (SCLA), X_ARDUINO_NANO_OU_STM32.9 (A5), X_ARDUINO_NANO_OU_STM32.23 (D5), X_I2C.P$4 (4), X_MEZZANINE.P$3 (3), X_RPI.P$5 (5)
I2C_SCL_5V: R6.1, U1.7 (SCLB), X_SIGNAUX.P$6 (6)
I2C_SDA: U1.3 (SDAA), X_ARDUINO_NANO_OU_STM32.8 (A4), X_ARDUINO_NANO_OU_STM32.22 (D4), X_I2C.P$3 (3), X_MEZZANINE.P$2 (2), X_RPI.P$3 (3)
I2C_SDA_5V: R5.1, U1.6 (SDAB), X_SIGNAUX.P$8 (8)
MESURE_VBAT: D22.3 (C1A2), R3.2, R4.1, X_ARDUINO_NANO_OU_STM32.7 (A3)
MISO: X_ARDUINO_NANO_OU_STM32.30 (D12), X_RPI.P$21 (21)
MOSI: X_ARDUINO_NANO_OU_STM32.29 (D11), X_RPI.P$19 (19)
unnamed: LED1.C, R1.2
unnamed: LED3.A, X_ARDUINO_NANO_OU_STM32.11 (A7)
unnamed: R71.2, X_ARDUINO_NANO_OU_STM32.20 (D2)
unnamed: R72.2, X_ARDUINO_NANO_OU_STM32.21 (D3)
unnamed: LED2.C, R2.2
unnamed: LED1.A, X_RPI.P$11 (11)
unnamed: R52.2, X_RPI.P$29 (29)
unnamed: R77.2, X_ARDUINO_NANO_OU_STM32.28 (D10)
unnamed: R51.2, X_RPI.P$31 (31)
unnamed: LED3.C, R76.2
unnamed: LED2.A, X_RPI.P$13 (13)
unnamed: R57.2, X_RPI.P$33 (33)
unnamed: R58.1, X_RPI.P$32 (32)
unnamed: R78.2, X_ARDUINO_NANO_OU_STM32.27 (D9)
unnamed: LED4.A, X_ARDUINO_NANO_OU_STM32.10 (A6)
unnamed: LED4.C, R75.2
PROPULSION_MCU: J_PROP.P$1 (1), R78.1
PROPULSION_RPI: J_PROP.P$3 (3), R58.2
PWM_DIRECTION: J_DIR.P$2 (2), X_SIGNAUX.P$5 (5)
PWM_PROPULSION: J_PROP.P$2 (2), X_SIGNAUX.P$3 (3)
RESET: X_ARDUINO_NANO_OU_STM32.18 (!RESET), X_MEZZANINE.P$6 (6)
RX_DIR: J_RX.P$2 (2), X_SIGNAUX.P$1 (1)
RX_MCU: J_RX.P$3 (3), R74.2, X_ARDUINO_NANO_OU_STM32.17 (RX/D0)
RX_MCU_P: R74.1, X_UART_MCU.P$2 (2)
RX_RPI: J_RX.P$1 (1), R54.1, X_RPI.P$10 (10)
RX_RPI_P: R54.2, X_UART_RPI.P$2 (2)
SCK: X_ARDUINO_NANO_OU_STM32.1 (D13), X_RPI.P$23 (23)
SERVO_DIR_MCU: J_DIR.P$1 (1), R77.1
SERVO_DIR_RPI: J_DIR.P$3 (3), R57.1
SS: X_RPI.P$24 (24)
TELEM_D: R24.2, X_SIGNAUX.P$4 (4)
TELEM_G: R20.2, X_SIGNAUX.P$10 (10)
TX_DIR: J_TX.P$2 (2), X_SIGNAUX.P$2 (2)
TX_MCU: J_TX.P$3 (3), R73.2, X_ARDUINO_NANO_OU_STM32.16 (TX/D1)
TX_MCU_P: R73.1, X_UART_MCU.P$1 (1)
TX_RPI: J_TX.P$1 (1), R53.1, X_RPI.P$8 (8)
TX_RPI_P: R53.2, X_UART_RPI.P$1 (1)
VCC_5V: R5.2, R6.2, U1.8 (VCCB), X_ALIM.P$3 (3_VCC), X_RPI.P$2 (2), X_RPI.P$4 (4)
VDD: D20.2 (C2), D22.2 (C2), D24.2 (C2), J_VDD.P$2 (2), U1.1 (VCCA), X_I2C.P$2 (2), X_MEZZANINE.P$1 (1), X_SIGNAUX.P$7 (7), X_UART_MCU.P$4 (4), X_UART_RPI.P$4 (4)
VDD_MCU: J_VDD.P$3 (3), X_ARDUINO_NANO_OU_STM32.2 (3V3)
VDD_RPI: J_VDD.P$1 (1), X_RPI.P$17 (17)
VS: R4.2, X_ALIM.P$1 (1_VS+), X_ARDUINO_NANO_OU_STM32.15 (VIN)

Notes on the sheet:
Drawn by:
Checked by:
CoVAPSy
Anthony Juton
v1.2
I2C Arduino
I2C Nucleo
Cavaliers MCU/RPI
Connecteur pour une carte Arduino Nano (testé avec Arduino nanon 33 IoT) ou une carte STM32 Nucleo (testé avec STM32L432KC mais doit fonctionner avec STM32G431KB également)
Connecteur Raspberry PI
Connecteur vers interface
Connecteur Microcontroleur
vers Mezzanine
Mesure tension bat
I2C et UART

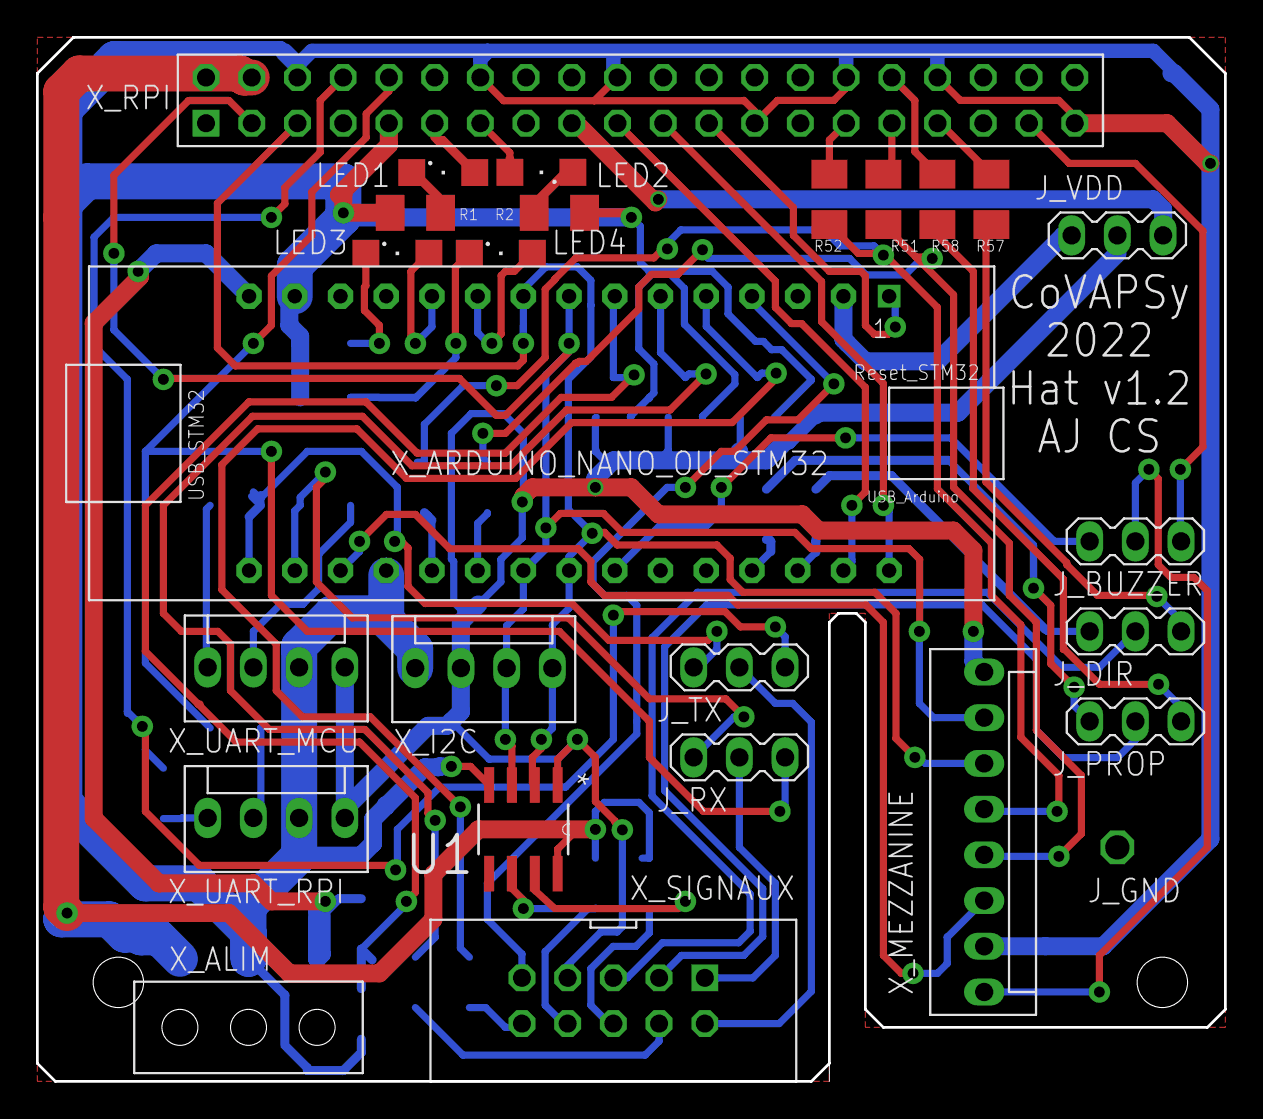
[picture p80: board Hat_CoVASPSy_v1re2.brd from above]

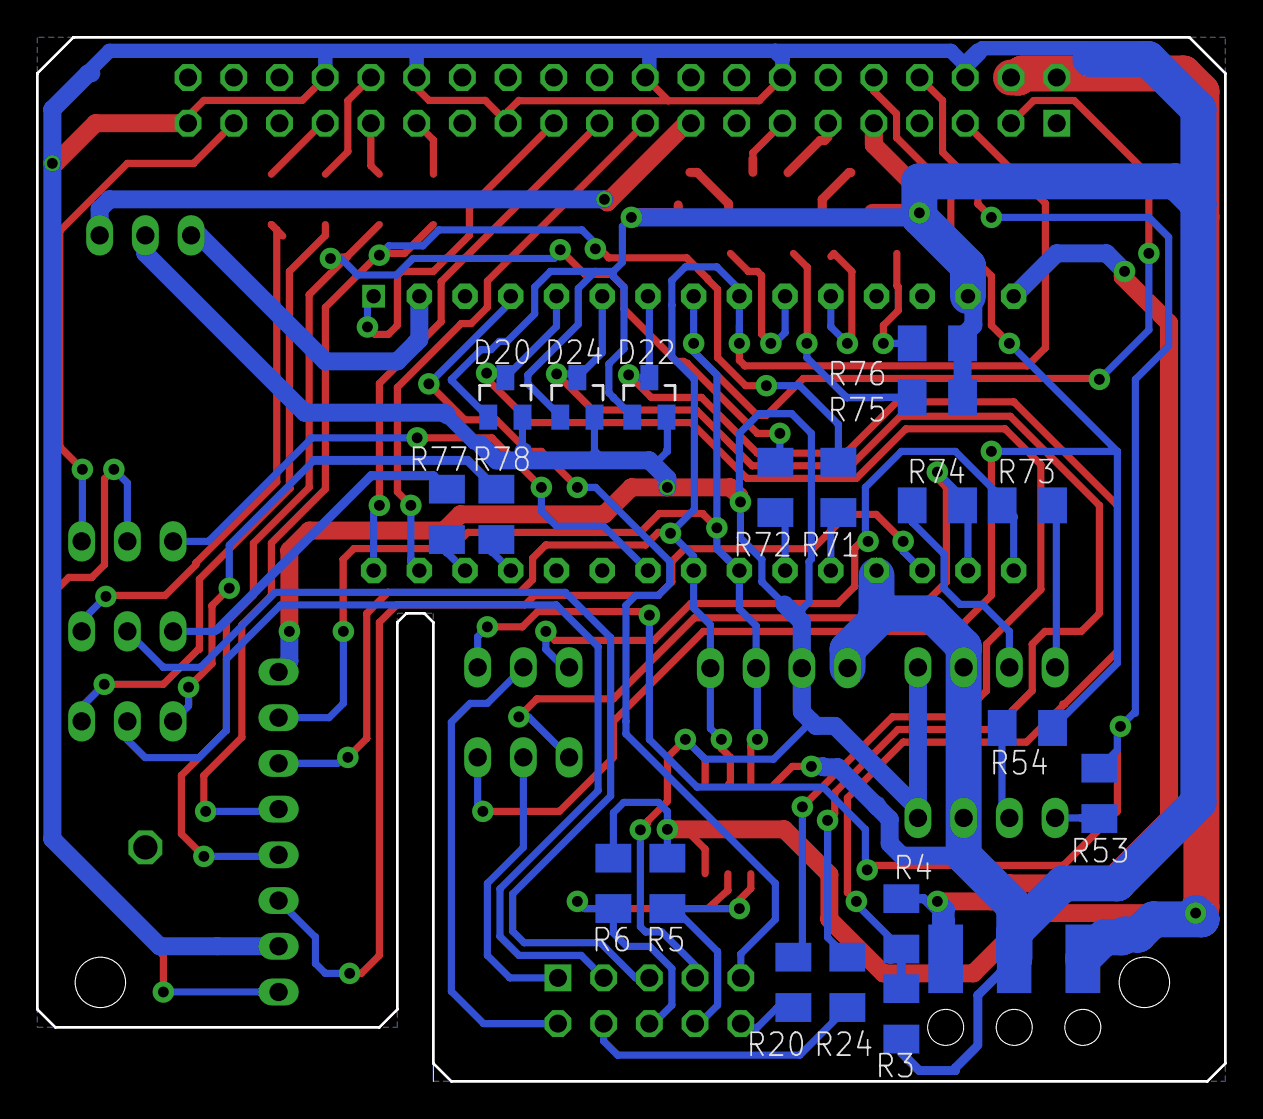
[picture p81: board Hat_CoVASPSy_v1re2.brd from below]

Board: 2 copper layers, 66.0 x 58.0 mm, 45 parts (19 on the bottom side), 57 nets.

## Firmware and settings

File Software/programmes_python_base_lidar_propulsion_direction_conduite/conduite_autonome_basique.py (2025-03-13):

from rplidar import RPLidar
import time
from rpi_hardware_pwm import HardwarePWM

#paramètres de la fonction vitesse_m_s
direction_prop = 1 # -1 pour les variateurs inversés ou un petit rapport correspond à une marche avant
pwm_stop_prop = 7.5
point_mort_prop = 0.4
delta_pwm_max_prop = 1.5 #pwm à laquelle on atteint la vitesse maximale

vitesse_max_m_s_hard = 8 #vitesse que peut atteindre la voiture
vitesse_max_m_s_soft = 2 #vitesse maximale que l'on souhaite atteindre


#paramètres de la fonction set_direction_degre
direction = -1 #1 pour angle_pwm_min a gauche, -1 pour angle_pwm_min à droite
angle_pwm_min = 5.5   #min
angle_pwm_max = 9.3   #max
angle_pwm_centre= 7.4

angle_degre_max = +18 #vers la gauche
angle_degre=0

pwm_prop = HardwarePWM(pwm_channel=0, hz=50)
pwm_prop.start(pwm_stop_prop)

def set_vitesse_m_s(vitesse_m_s):
    if vitesse_m_s > vitesse_max_m_s_soft :
        vitesse_m_s = vitesse_max_m_s_soft
    elif vitesse_m_s < -vitesse_max_m_s_hard :
        vitesse_m_s = -vitesse_max_m_s_hard
    if vitesse_m_s == 0 :
        pwm_prop.change_duty_cycle(pwm_stop_prop)
    elif vitesse_m_s > 0 :
        vitesse = vitesse_m_s * (delta_pwm_max_prop)/vitesse_max_m_s_hard
        pwm_prop.change_duty_cycle(pwm_stop_prop + direction_prop*(point_mort_prop + vitesse ))
    elif vitesse_m_s < 0 :
        vitesse = vitesse_m_s * (delta_pwm_max_prop)/vitesse_max_m_s_hard
        pwm_prop.change_duty_cycle(pwm_stop_prop - direction_prop*(point_mort_prop - vitesse ))
        
def recule():
    set_vitesse_m_s(-vitesse_max_m_s_hard)
    time.sleep(0.2)
    set_vitesse_m_s(0)
    time.sleep(0.2)
    set_vitesse_m_s(-1)
    
pwm_dir = HardwarePWM(pwm_channel=1,hz=50)
pwm_dir.start(angle_pwm_centre)

def set_direction_degre(angle_degre) :
    global angle_pwm_min
    global angle_pwm_max
    global angle_pwm_centre
    angle_pwm = angle_pwm_centre + direction * (angle_pwm_max - angle_pwm_min) * angle_degre /(2 * angle_degre_max )
    if angle_pwm > angle_pwm_max : 
        angle_pwm = angle_pwm_max
    if angle_pwm < angle_pwm_min :
        angle_pwm = angle_pwm_min
    pwm_dir.change_duty_cycle(angle_pwm)
    
#connexion et démarrage du lidar
lidar = RPLidar("/dev/ttyUSB0",baudrate=256000)
lidar.connect()
print (lidar.get_info())
lidar.start_motor()
time.sleep(1)

tableau_lidar_mm = [0]*360 #création d'un tableau de 360 zéros


try : 
    for scan in lidar.iter_scans(scan_type='express') : 
    #Le tableau se remplissant continuement, la boucle est infinie
        #rangement des données dans le tableau
        for i in range(len(scan)) :
            angle = min(359,max(0,359-int(scan[i][1]))) #scan[i][1] : angle 
            tableau_lidar_mm[angle]=scan[i][2]  #scan[i][2] : distance    
        #############################################
        ## Code de conduite (issu du simulateur ou non)
        #############################################
            
        #l'angle de la direction est la différence entre les mesures  
        #des rayons du lidar à -60 et +60°  
        angle_degre = 0.02*(tableau_lidar_mm[60]-tableau_lidar_mm[-60])
        set_direction_degre(angle_degre)
        vitesse_m_s = 0.5
        set_vitesse_m_s(vitesse_m_s)    
        ##############################################
except KeyboardInterrupt: #récupération du CTRL+C
    print("fin des acquisitions")

#arrêt et déconnexion du lidar et des moteurs
lidar.stop_motor()
lidar.stop()
time.sleep(1)
lidar.disconnect()
pwm_dir.stop()
pwm_prop.start(pwm_stop_prop)

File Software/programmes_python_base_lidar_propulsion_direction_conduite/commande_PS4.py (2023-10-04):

from pyPS4Controller.controller import Controller
from rpi_hardware_pwm import HardwarePWM
import time

###################################################
#Intialisation des moteurs
##################################################
#paramètres de la fonction vitesse_m_s, à étalonner
direction_prop = -1# -1 pour les variateurs inversés ou un petit rapport correspond à une marche avant
pwm_stop_prop = 8.10
point_mort_prop = 0.46
delta_pwm_max_prop = 1.5 #pwm à laquelle on atteint la vitesse maximale

vitesse_max_m_s_hard = 8 #vitesse que peut atteindre la voiture
vitesse_max_m_s_soft = 2 #vitesse maximale que l'on souhaite atteindre

direction = -1 #1 pour angle_pwm_min a gauche, -1 pour angle_pwm_min à droite
angle_pwm_min = 6.2   #min
angle_pwm_max = 8.5   #max
angle_pwm_centre= 7.35
angle_degre_max = +18 #vers la gauche
angle_degre=0

pwm_prop = HardwarePWM(pwm_channel=0, hz=50)
pwm_dir = HardwarePWM(pwm_channel=1, hz=50)
print("PWM désactivées")

def set_direction_degre(angle_degre) :
    global angle_pwm_min
    global angle_pwm_max
    global angle_pwm_centre
    angle_pwm = angle_pwm_centre + direction * (angle_pwm_max - angle_pwm_min) * angle_degre /(2 * angle_degre_max )
    if angle_pwm > angle_pwm_max : 
        angle_pwm = angle_pwm_max
    if angle_pwm < angle_pwm_min :
        angle_pwm = angle_pwm_min
    pwm_dir.change_duty_cycle(angle_pwm)
    
def set_vitesse_m_s(vitesse_m_s):
    if vitesse_m_s > vitesse_max_m_s_soft :
        vitesse_m_s = vitesse_max_m_s_soft
    elif vitesse_m_s < -vitesse_max_m_s_hard :
        vitesse_m_s = -vitesse_max_m_s_hard
    if vitesse_m_s == 0 :
        pwm_prop.change_duty_cycle(pwm_stop_prop)
    elif vitesse_m_s > 0 :
        vitesse = vitesse_m_s * (delta_pwm_max_prop)/vitesse_max_m_s_hard
        pwm_prop.change_duty_cycle(pwm_stop_prop + direction_prop*(point_mort_prop + vitesse ))
    elif vitesse_m_s < 0 :
        vitesse = vitesse_m_s * (delta_pwm_max_prop)/vitesse_max_m_s_hard
        pwm_prop.change_duty_cycle(pwm_stop_prop - direction_prop*(point_mort_prop - vitesse ))
        
def recule():
    set_vitesse_m_s(-vitesse_max_m_s_hard)
    time.sleep(0.2)
    set_vitesse_m_s(0)
    time.sleep(0.2)
    set_vitesse_m_s(-1)


a_prop = vitesse_max_m_s_soft/(65198)
a_dir=(angle_degre_max)/(-32767)

class MyController(Controller):

    def __init__(self, **kwargs):
        Controller.__init__(self, **kwargs)
        
    def on_R2_press(self,value):
        print("La valeur de R2 est: ",value)
        value += 32767
        set_vitesse_m_s(a_prop*value)
        
    def on_R2_release(self):
         #print("Arrêt complet")
         set_vitesse_m_s(0)
 
    def on_L3_x_at_rest(self):
        set_direction_degre(0)
        
    def on_R1_press(self):
        recule()
        
    def on_R1_release(self):
        set_vitesse_m_s(0)
    
    def on_L3_right(self,value):
        set_direction_degre(a_dir*value)

    def on_L3_left(self,value):
        set_direction_degre(a_dir*value)
        
    def on_L2_press(self, value):
        set_vitesse_m_s(-vitesse_max_m_s_hard)
        
    def on_L2_release(self):
        set_vitesse_m_s(0)
        
    def on_x_press(self):
        pwm_prop.stop()
        pwm_dir.stop()
        print("PWM désactivées")
        
    def on_circle_press(self):
        pwm_prop.start(pwm_stop_prop)
        pwm_dir.start(angle_pwm_centre)
        print("PWM activées")


controller = MyController(interface="/dev/input/js0", connecting_using_ds4drv=False)
controller.listen()

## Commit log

2021-06-22 ajout des videos
2021-06-22 ajout de matériel et Photos
2021-06-22 ajout de docs
2021-06-22 Ajout de l'image de la voiture de Gauthier
2022-08-25 ajout des CR de réunion
2022-08-26 Ajout de photos et videos
2022-08-26 ajout des photos
2022-08-26 ajout des vidéos
2022-08-29 ajout d'éléments dans Matériel et des CR de réunion dans docs
2022-08-29 ajout des images 3D de la voiture dans Materiel
2022-10-28 ajout de l'exemple d'apprentissage par renforcement sous webots avec Altino
    [circuit 2 v3.obj, circuit 2 v4.obj, circuit4 v2.2.obj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]
2022-10-28 ajout des images DALL-E
2022-10-28 ajout de quelques photos
2022-11-17 Ajout des modèles 3D des bords de piste
    [ImageToStl.com_bloc_1m.obj, ImageToStl.com_virage.obj]
2022-11-25 Ajout des cartes électroniques (Schéma, PCB, PDF)
    [Hat_CoVASPSy_v1re2.brd, Hat_CoVASPSy_v1re2.sch, Interface_CoVASPSy_v1re2.brd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]
2022-12-14 ajout du bloc 0.5m
    [ImageToStl.com_bloc_0.5m.obj]
2022-12-15 ajout de la piste 2022
    [circuit 2 v3.obj, circuit 2 v4.obj, circuit4 v2.2.obj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]
2023-01-11 ajout des programmes de test arduino
2023-01-20 Add files via upload
    Ajout des guides pour le montage des cartes électroniques
2023-01-25 ajout du simulateur ENS Webots R2022b avec TT02 et éléments de piste
    [ImageToStl.com_bloc_0.5m.obj, ImageToStl.com_bloc_1m.obj, ImageToStl.com_virage.obj]
2023-01-25 Ajout des photos de la voiture type version janvier 2023
2023-01-25 mise à jour de la page web
2023-01-26 remise en ligne des éléments de piste
    [ImageToStl.com_bloc_0.5m.obj, ImageToStl.com_bloc_1m.obj, ImageToStl.com_virage.obj]
2023-01-26 Modification de la photo de la voiture avec carrosserie
2023-01-27 Ajout CAO
    [Carter pignon support fourche.stp, Pare-choc arrière.stp, Pignon intermediaire 70dts.dxf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]
2023-02-01 Mise à jour des références matérielles, mise en ordre du dossier matériel
    [Carter pignon support fourche.stp, Pare-choc arrière.stp, Pignon intermediaire 70dts.dxf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]
2023-02-01 Mise en ordre du dossier Pièces matérielles
    [Carter pignon support fourche.stp, Pare-choc arrière.stp, Pignon intermediaire 70dts.dxf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]
2023-02-01 Ajout d'un simulateur avec les élements pour construire une piste personnalisée et avec 2 voitures
2023-02-08 Ajoute des fiches de mises en oeuvre STM32
2023-02-08 MAJ de la fiche SPI
2023-02-22 Rename 011.1-Plaque trouée.dxf to Plaque trouée.dxf
    [Plaque trouée.dxf]
2023-02-22 Rename 011.2-Plaque trouée supérieure.dxf to Plaque trouée supérieure.dxf
    [Plaque trouée supérieure.dxf]
2023-03-06 mise à jour doc SPI STM32
2023-03-13 Fichier de découpe pignon intermédiaire
    [014.7.2-Pignon intermediaire 70dts CDR.dxf]
2023-04-13 Ajout des présentations des voitures
2023-08-23 ajout du projet de base Webots 2023b
2023-08-24 ajout des programmes python de base
2023-08-24 retrait de numpy du contrôleur de base pour webots
2023-10-04 MAJ des prog python de base
2023-10-04 ajout du dossier pour les fichiers c
2023-12-13 ajout des bibliothèques C
2024-01-13 modif des bibliotheques python
2024-01-17 MAJ des pièces du kit et guide d'assemblage
2024-01-18 Ajout du programme capteurs/écran pour la STM32
2024-01-28 Create Voiture STM32
2024-03-07 MAJ du tutoriel installation de la RPI
2024-03-29 ajout du programme pour homologuer la détection des voitures
2025-06-25 MAJ de la page web
2025-09-15 Un peu de rangement
    [Carter pignon support fourche.stp, Gabarit de découpe voiture.DXF, Hat_CoVASPSy_v1re2.brd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]
2025-09-15 MAJ du site
    [Carter pignon support fourche.stp, Gabarit de découpe voiture.DXF, Hat_CoVASPSy_v1re2.brd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]
2026-01-14 Ajout du programme de lecture de la vitesse de la voiture

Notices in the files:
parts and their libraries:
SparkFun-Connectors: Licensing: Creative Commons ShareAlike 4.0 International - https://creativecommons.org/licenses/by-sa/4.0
